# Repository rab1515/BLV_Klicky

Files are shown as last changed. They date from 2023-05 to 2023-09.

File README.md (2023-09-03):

# BLV_Klicky
Kicky probe and purge bucket implementation for the metal kit BLV cube

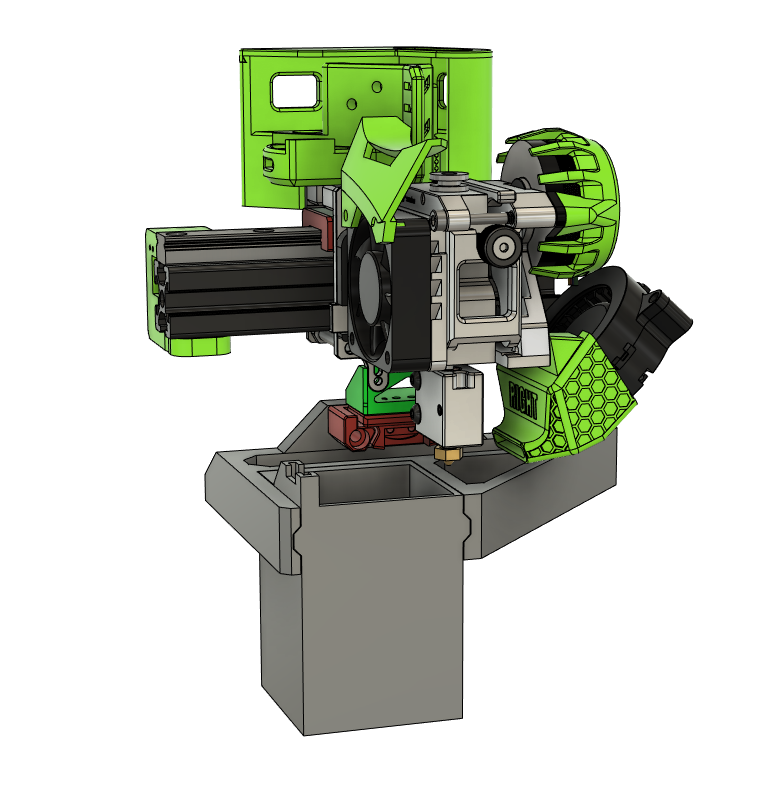
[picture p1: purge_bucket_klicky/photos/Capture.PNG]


This probe is designed to fit the metal kit, with the NFSunrise hotend, most hotends will also work as well.

# Print Settings
Print in the orientation shown below:
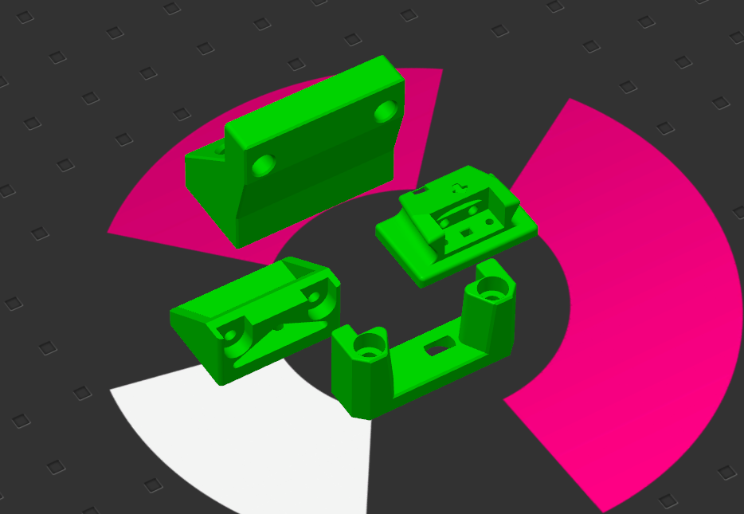
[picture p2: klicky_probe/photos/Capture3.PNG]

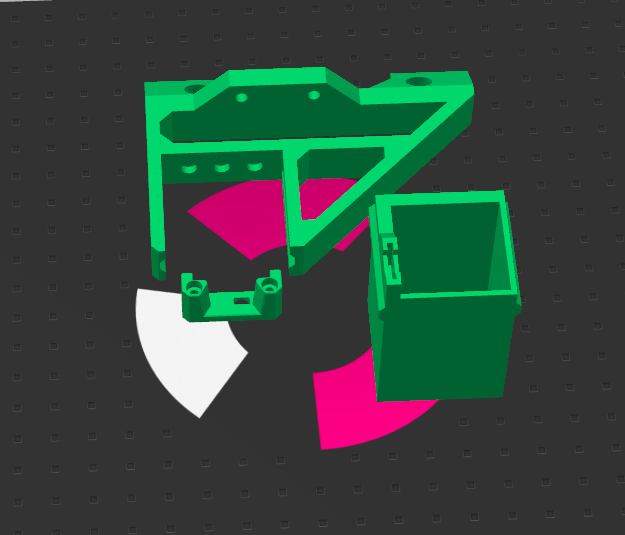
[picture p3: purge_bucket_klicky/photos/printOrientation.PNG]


# Hardware

To assemble the probe you will need:

* 8 6mmx3mm neodymium magnets
* 2 m2x8mm socket head screws  
* 2 m3x16mm socket head screws
* 2 m3x6mm threaded inserts
* 2 m5x10 socket head screws
* 2 m5 t-nuts
* 2 m2x8mm socket head screws
* 2 m2 nuts

The threaded inserts get inserted into the probe dock base, everything else is pretty self-explanatory.

Please reference the Klicky repo for probe assembly instructions: https://github.com/jlas1/Klicky-Probe

To assemble the purge bucket, glue and press 3x 3mmx6mm neodymium magnets to the bucket, then glue and place 3x magnets in the bracket, making sure to match polarity.
The bucket bracket gets attached to the back rail using 2x m5x10 socket head screws and t-nuts. Cut a piece of 2mm thick silicone to 15mm by 13mm and place it in the slot of the purge bucket.

# Software

The macros were written for RepRap firmware 3.4.5, previous versions may not work.

These macros are intended to be an example, and might need to be modified for your printer.

Create a folder in the `Macros` directory called `Docking`. Place `deployProbe`, `stowProbe`, and `DockEnv` into that folder. If using the purge bucket, do the same for the purge bucket macros placing them a created `PurgeBucket` folder.

Edit `DockEnv` to change the `onDock_x` and `onDock_y` to match your docks mounted location. It WILL need to be on the back wall with room to the negative X direction to work with out modification. If necessary you can flip the sign on the `sideDock_x` variable. If using the purge bucket edit the `PurgeBucketEnv` macro and set `inBox_x` `inBox_y`.

add `M98 P"0:/macros/Docking/DockEnv"` to your `config.g`. This will load the variables that define where your dock is. While editing the `config.g` update your z probe config, I pluged my probe into `Z_PROBE_IN` so my config was `M558 P5 C"zprobe.in" H3 F300 T99999`. If useing the purge bucket, add `M98 P"0:/macros/PurgeBucket/PurgeBucketEnv"` to your `config.g`

Edit your `homeall.g` AND your `homez.g` in your system folder to reflect the new z probe. My `homeall.g` calls `homez.g` and are provided as an example.

Restart your board for changes to take effect, and test out the macros. Should  `deployProbe` or `stowProbe` fail mechanically, there is logic to disable steppers and prevent any further movement. 

`repeatability test` runs 30 docks/undocks with a move in between to test repeatability of the probe. My installation gave a maximum deviation of 0.013 mm with a standard deviation of 0.003 mm .

# Purge Bucket config

To use the purge bucket, use the `moveToPurgeBucket` and `wipe` macros inside your start/pause gcode. Mine are proveded as an example. I split my pre starting gcode into 2 seprate files,  `startPrintPostHeat.g` and `startPrintPreHeat.g`. My slicer start gcode is set to: 
```
M98 P"0:/sys/startPrintPreHeat.g"
M140 S60.0 ;Start heating bed
M190 S60.0 ;Wait for bed to reach temp before proceeding
M104 S230 ;Start heating extruder
M109 S230 ;Wait for extruder to reach temp before proceeding
M98 P"0:/sys/startPrintPostHeat.g"
```

See also my pause and resume macros.

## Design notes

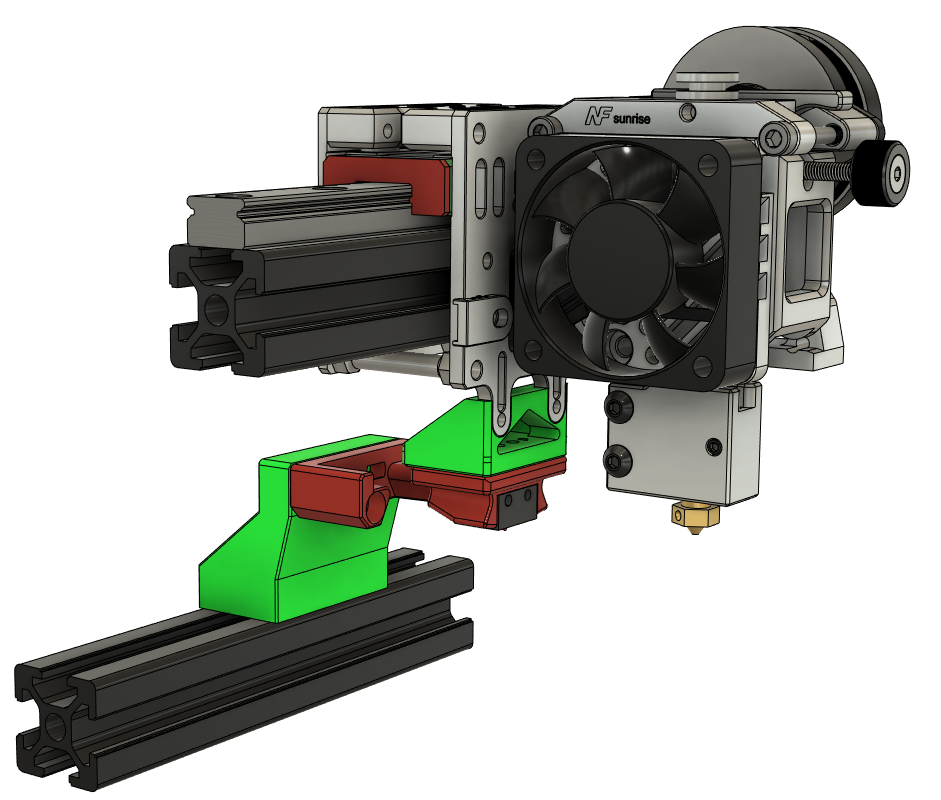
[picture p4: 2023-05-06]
klicky_probe/photos/Capture1.PNG

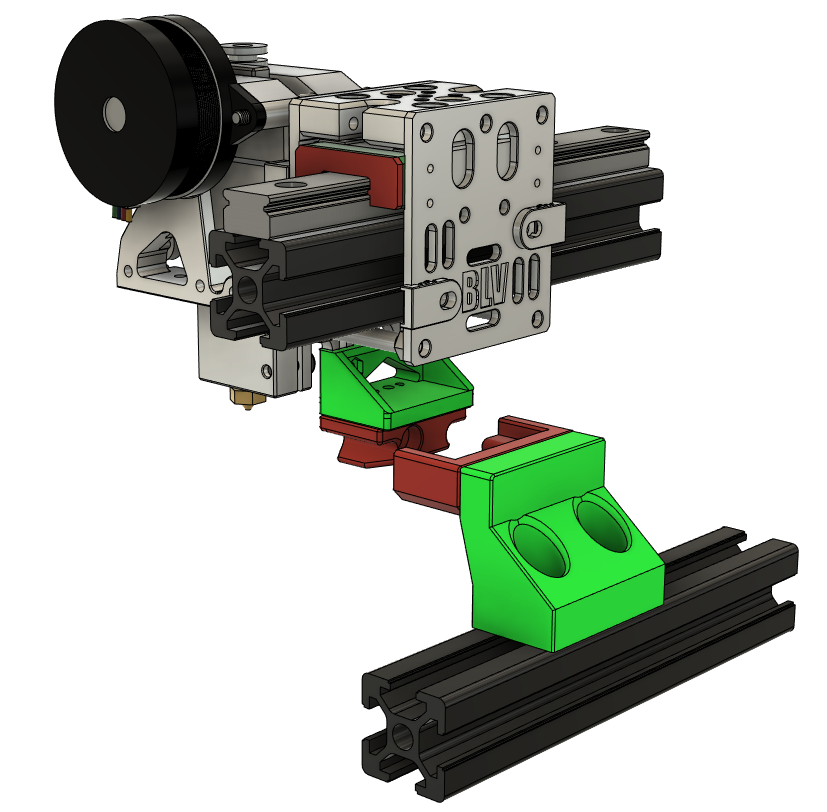
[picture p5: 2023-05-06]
klicky_probe/photos/Capture2.PNG

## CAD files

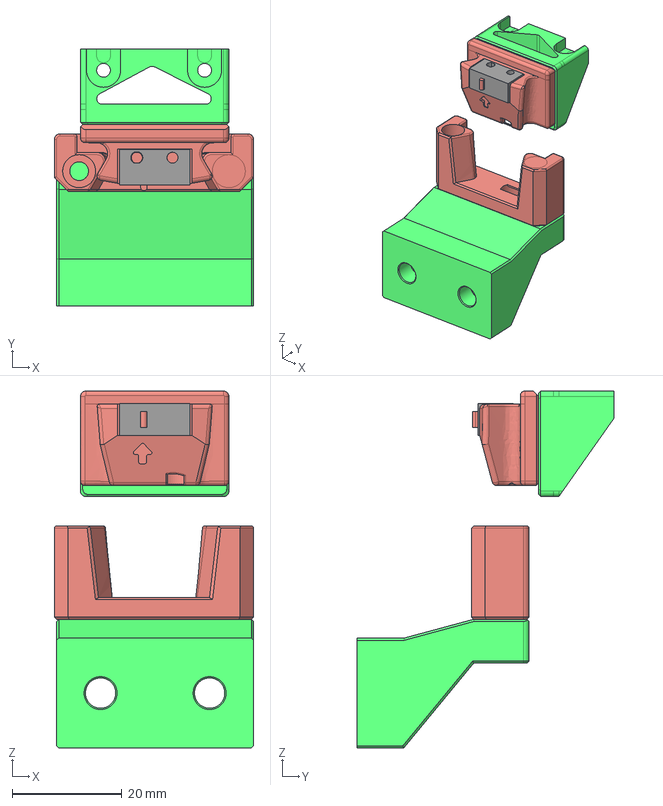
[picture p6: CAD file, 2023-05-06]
klicky_probe/CAD/BLV_Klicky_Combined.step
36.3 x 46.8 x 65.0 mm
Probe Dock v2.1
D2F_ACTUATOR
D2F_BASE

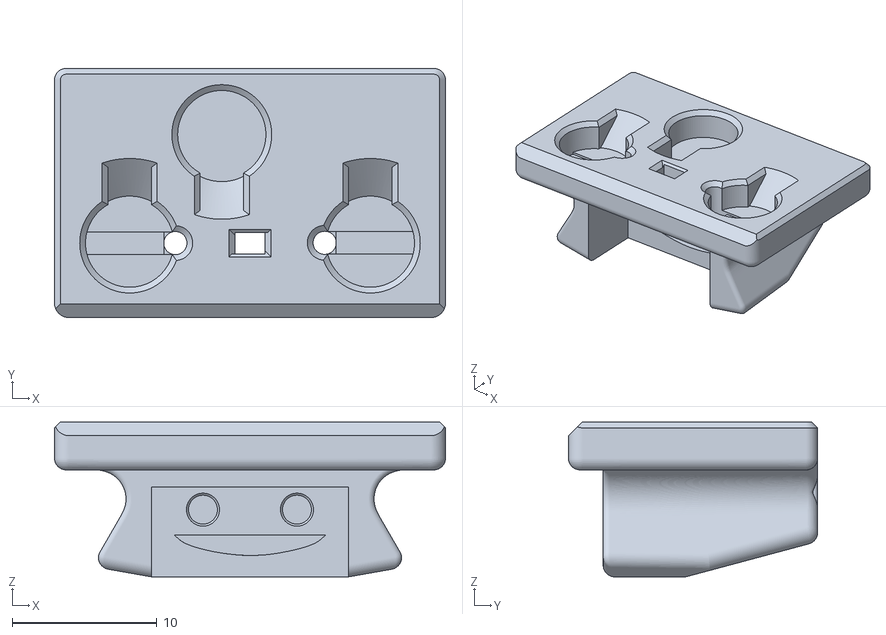
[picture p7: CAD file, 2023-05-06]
klicky_probe/STL/KlickyProbe.stl
27.0 x 17.2 x 10.7

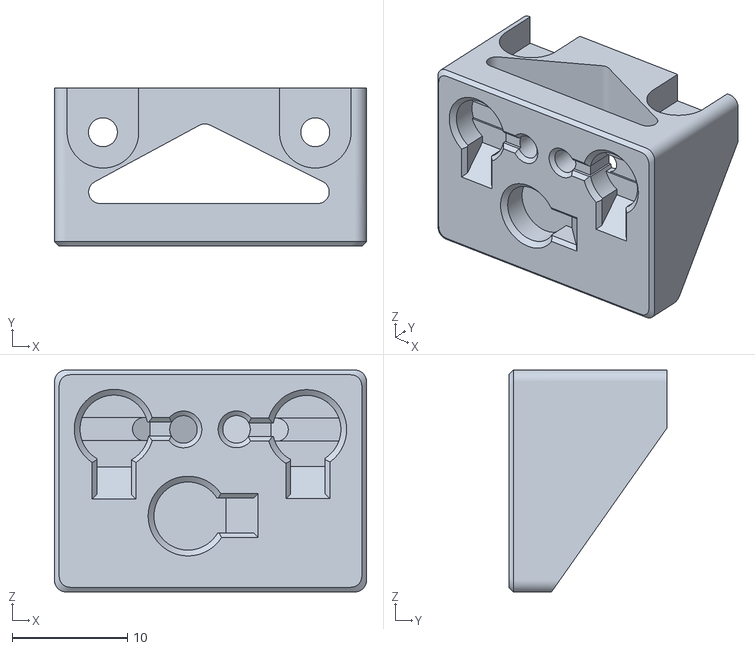
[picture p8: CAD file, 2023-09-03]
purge_bucket_klicky/STL/klickyProbeHolder.stl
27.0 x 13.7 x 19.2

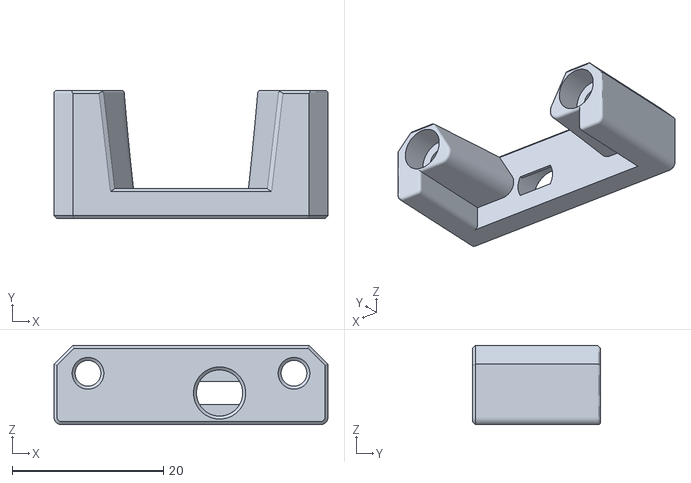
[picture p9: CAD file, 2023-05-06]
klicky_probe/STL/ProbeDock.stl
36.3 x 17.0 x 10.5

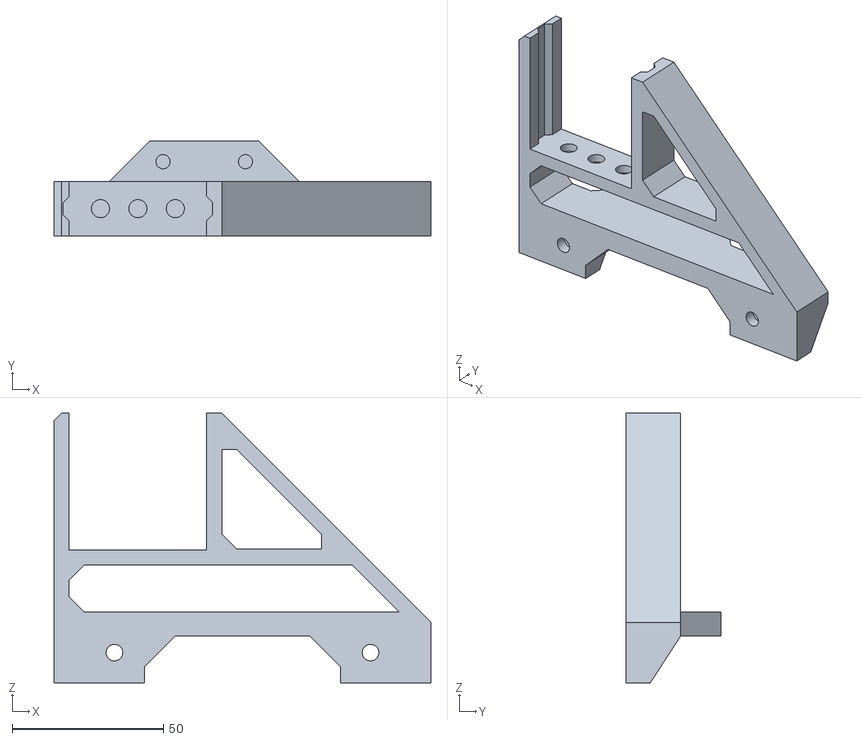
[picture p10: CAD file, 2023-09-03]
purge_bucket_klicky/STL/bucketBracket.stl
124.7 x 31.3 x 89.2

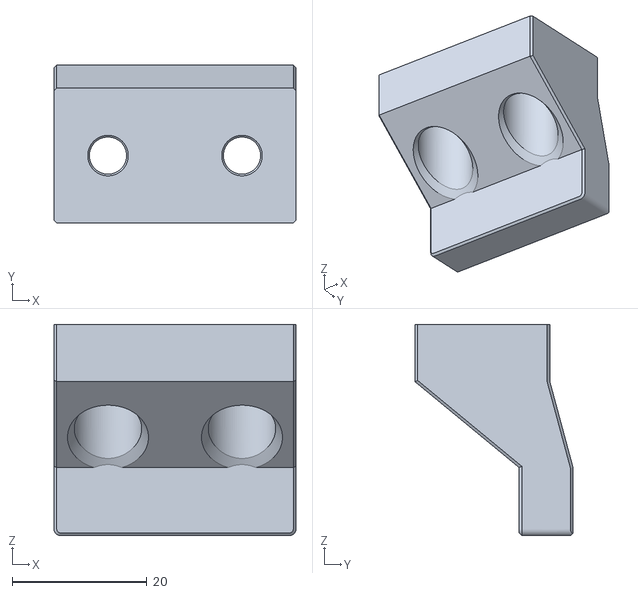
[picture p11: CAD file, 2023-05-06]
klicky_probe/STL/ProbeDockBase.stl
35.9 x 23.4 x 31.3

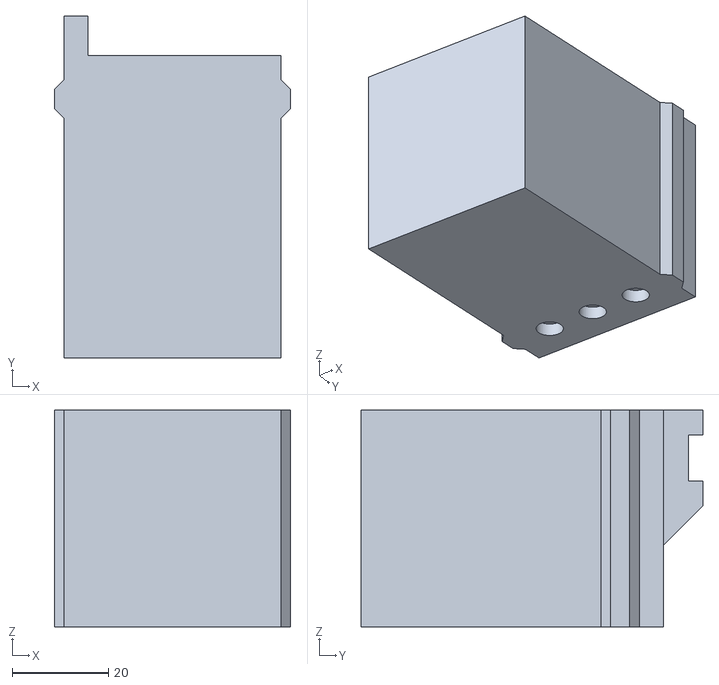
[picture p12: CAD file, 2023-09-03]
purge_bucket_klicky/STL/purgeBucket.stl
49.0 x 70.9 x 45.0

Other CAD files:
klicky_probe/STL/KlickyProbeMount.stl
purge_bucket_klicky/STL/klickyDock.stl
purge_bucket_klicky/STL/klicky probe Body.stl

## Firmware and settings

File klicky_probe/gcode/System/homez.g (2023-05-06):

; homez.g
; called to home the Z axis
;
; generated by RepRapFirmware Configuration Tool v3.2.3 on Sun Mar 14 2021 16:28:18 GMT-0400 (Eastern Daylight Time)
G91							; relative posision
G1 H4 Z5 F99999         	; lift Z relative to current position
G90							; absolute posisioning


M98 P"0:/macros/Docking/deployProbe"
G0 X155 Y155 F99999			; bed center
M558 F600					; set Z probe speed fast
G30							; probe at current pos
M558 F120					; set Z probe speed slow
G30							; probe at current pos

G91							; relative posision
G1 H4 Z5 F99999         	; lift Z relative to current position
G90	

M98 P"0:/macros/Docking/stowProbe"

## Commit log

2023-05-06 added build plate photo
2023-05-06 inital cad commit
    [BLV_Klicky_Combined.step, KlickyProbe.stl, KlickyProbeMount.stl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]
2023-09-03 added purge bucket
    [BLV_Klicky_Combined.step, KlickyProbe.stl, KlickyProbeMount.stl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]
2023-09-03 added pause resume macros
    [pause.g, resume.g]
